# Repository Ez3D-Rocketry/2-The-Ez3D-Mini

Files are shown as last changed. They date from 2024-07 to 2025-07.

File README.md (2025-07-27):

# Ez3D-Mini

- Great park flyer that uses mini A motors
- Parts tape together
- No glue required

# Parts List:
1. Ez3D-1350-4 Fin Can
2. BT-50 Nose Cone
3. 13mm Retainer Cap
   - Print out the multiple sizes (No scaling, +3%, +5%), These account for different printing tolerances and post flight shrinking.
4. Six (6) inches of BT-50 type body tube
   - A standard 18 inch tube makes three kits
   - 3D printable tube cutting guide included in repository files
5. Three (3) feet of Kevlar string for Recovery Harness
   - Flight tested on 9KM DWLIFE Black Braided Kevlar Cord (1.3mm, 300 lb) but others may work
6. Twelve (12) inches of streamer (Optional)
7. Tape



# Assembly: 
     
1. Tie Recovery Harness to hole in Fin Can
2. Thread Recovery Harness thru Body Tube
3. Slide Body Tube onto top of Fin Can
4. Tape Body Tube to Fin Can - avoid blocking integrated launch lug
5. Tie loose end of Recovery Harness to Nose Cone
6. Tie streamer to Recovery Harness near top of Nose Cone

**NOTE: Individual printers and filament have different tolerances** <br />
**- Fit check items before assembly. Options to adjust if necessary:**
- Add tape to increase diameter
- Remove material by sanding
- If your printer has a scaling feature, use it to adjust the part size
- Change the dimensions in the FreeCAD file



# Launch Preparation:
1. Insert 1 or 2 squares of recovery wadding into Body Tube
2. Load Recovery Harness and Streamer into Body Tube
3. Place Nose Cone on top of Body Tube - ensure slightly snug fit
4. Load motor into Fin Can
5. Screw Motor Retention Cap onto base of Fin Can
   - Depending on your printer, the larger sizes may fit better
   - After a flight or two, the smaller size may fit better
6. Launch using standard model rocket procedures

# Recommended motors and expected performance: 

1/2A3-2T   = 93 ft  (Optimum delay = 2 s)

A10-3T      = 240 ft (Optimum delay = 2.95 s)

A3-4T       = 273 ft (Optimum delay = 3.3 s)

# IMPORTANT POST FLIGHT NOTES:
- 3D printed material shrinks after cooling down from heat of motor
- Removal of motor may be difficult or impossible after one or several flights
- The smaller motor retainer cap may fit better after the first flight
- If existing motor retainer caps no longer work, friction or tape may suffice for retention
- PLA filament most suspectable to shrinking. Others may last longer.

## Entire kit fits in a Ziplock sandwich bag!



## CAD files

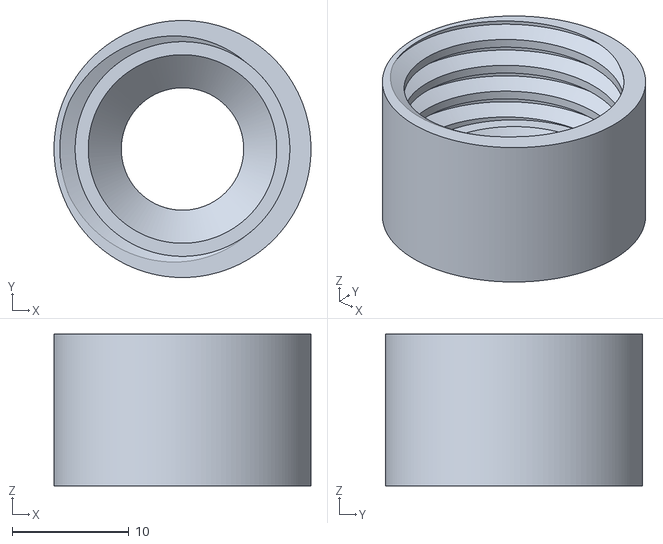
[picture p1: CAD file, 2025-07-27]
3D Printing Files/13mm Retainer Cap M20x2-13mmTall x1.05 in X and Y.stl
22.0 x 22.0 x 13.0

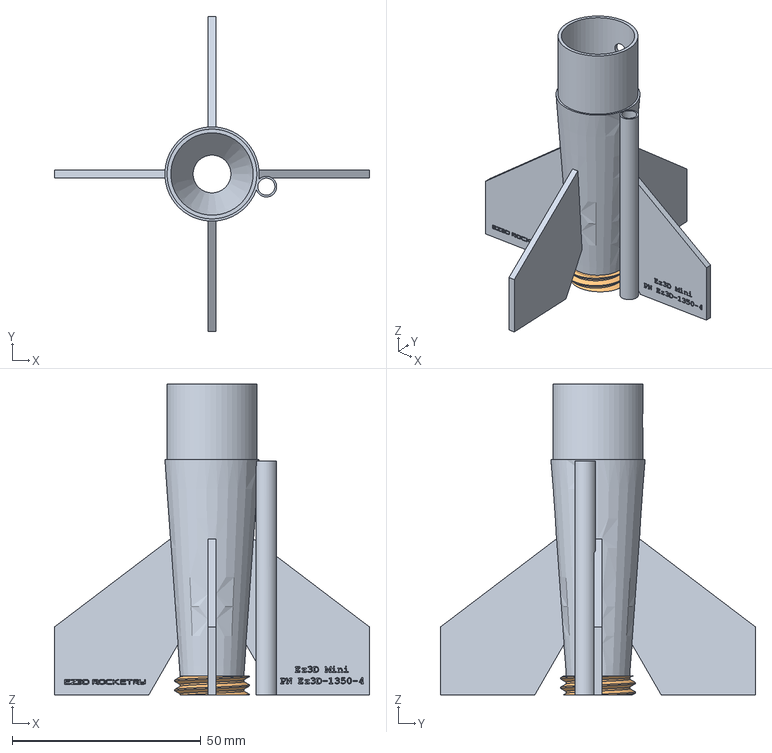
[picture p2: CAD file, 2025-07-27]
FreeCAD Files/Ez3D-1350-4 Fin Can.FCStd
83.5 x 83.5 x 82.3 mm
13mmThread20x2.5-5mmTall

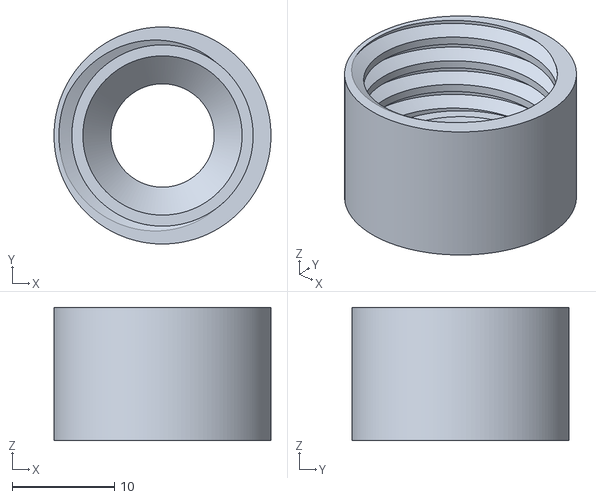
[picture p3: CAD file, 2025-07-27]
3D Printing Files/13mm Retainer Cap M20x2-13mmTall x1.01in X and Y.stl
21.2 x 21.2 x 13.0

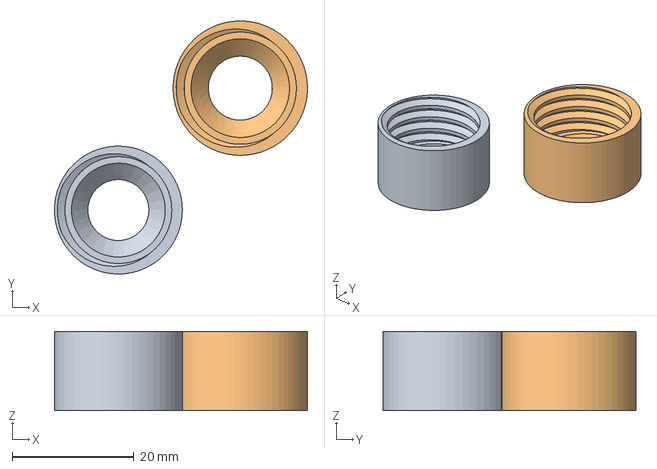
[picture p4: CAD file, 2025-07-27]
FreeCAD Files/13mm Retainer Cap M20x2-13mmTall.FCStd
41.5 x 41.5 x 13.0 mm
Use this Clone to make scaled up versions

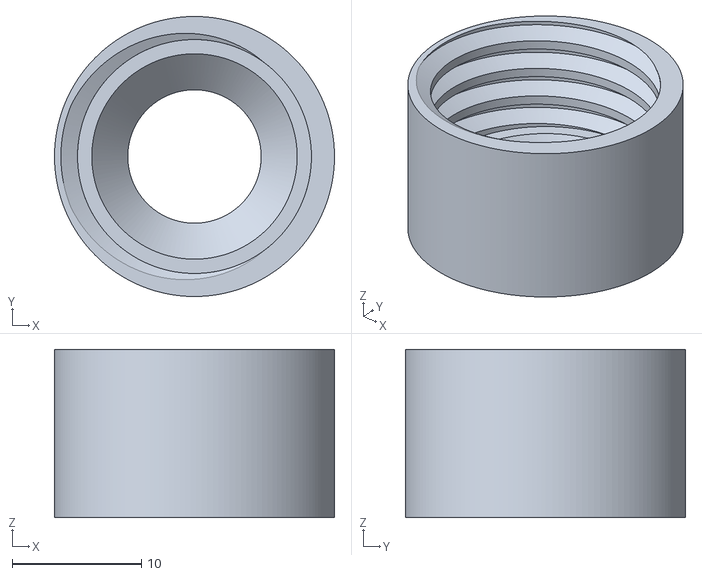
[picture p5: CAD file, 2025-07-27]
3D Printing Files/13mm Retainer Cap M20x2-13mmTall x1.03 in X and Y.stl
21.6 x 21.6 x 13.0

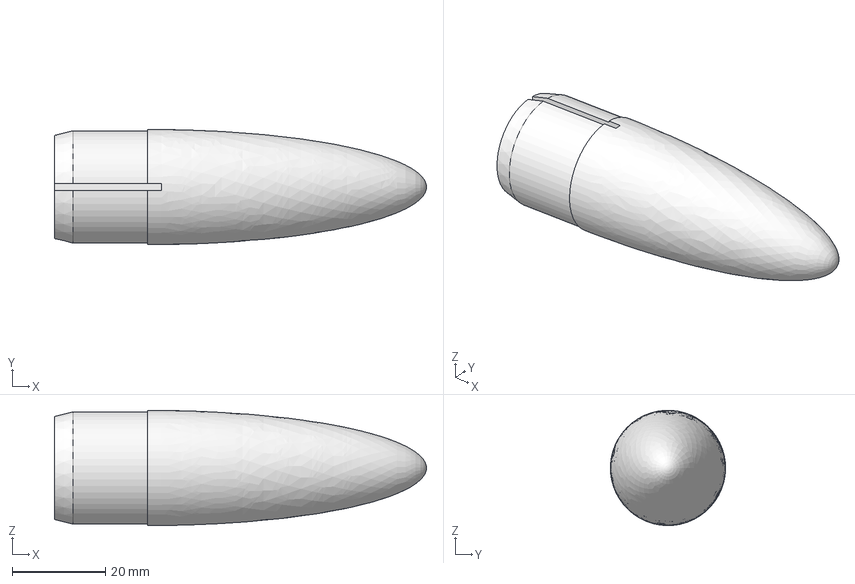
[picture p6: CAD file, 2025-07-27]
FreeCAD Files/BT50 Nose Cone - Elliptical, Hollow, with slot.FCStd
80.0 x 24.8 x 24.8 mm

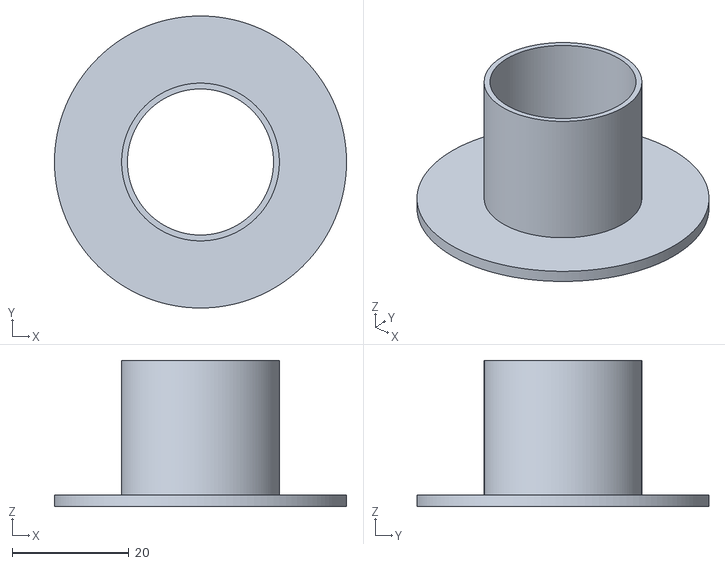
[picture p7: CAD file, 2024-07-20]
3D Printing Files/BT50 Tube Cutting Guide.stl
50.0 x 50.0 x 25.0

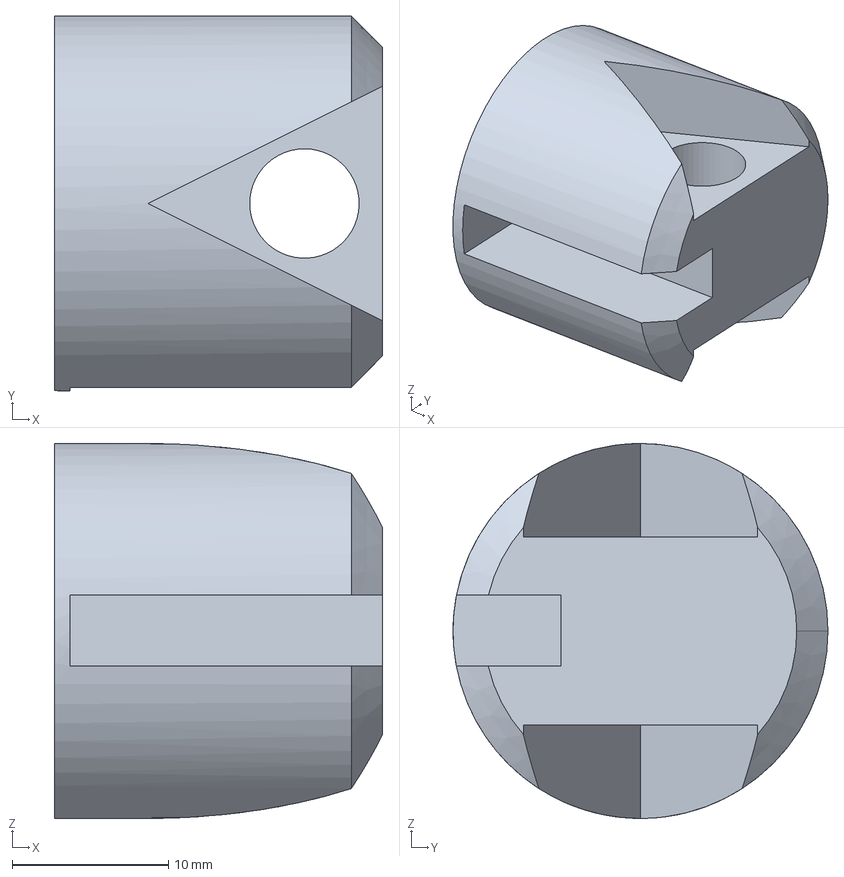
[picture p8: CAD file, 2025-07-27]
FreeCAD Files/BT50 Nose Cone - Elliptical, Solid, with slot.FCStd
21.0 x 24.0 x 24.0 mm

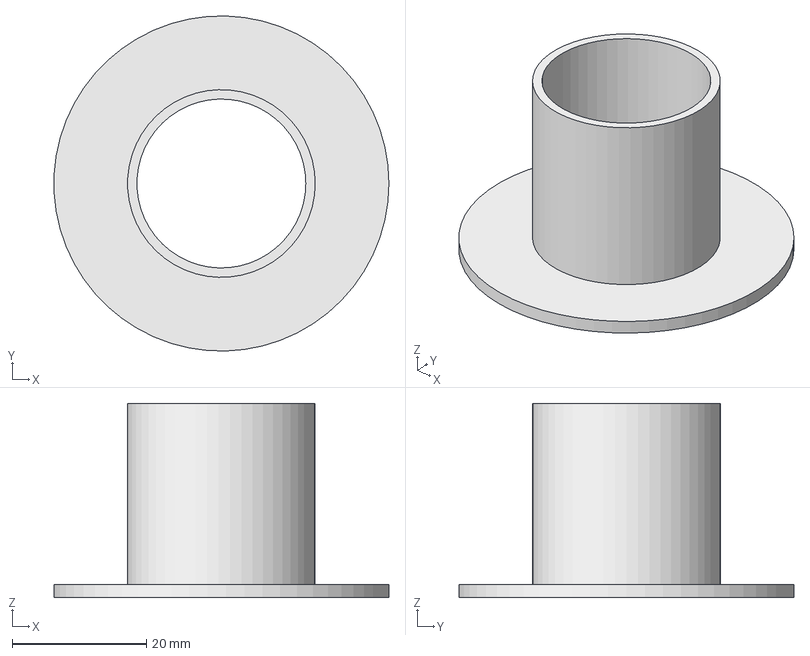
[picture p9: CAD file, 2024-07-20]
FreeCAD Files/BT50 Tube Cutter Guide.FCStd
50.0 x 50.0 x 29.0 mm

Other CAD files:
3D Printing Files/BT50 Nose Cone - Elliptical, Hollow, with slot.stl
3D Printing Files/BT50 Nose Cone - Elliptical, Solid, with slot.stl
3D Printing Files/Ez3D-1350-4 Fin Can.stl

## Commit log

2024-07-20 Rename BT50 Tube Cutter Guide.FCStd to _BT50 Tube Cutter Guide.FCStd
    [_BT50 Tube Cutter Guide.FCStd]
2024-07-20 BT-50 Cutting Guide FreeCAD file
    [BT50 Tube Cutter Guide.FCStd]
2024-07-20 BT-50 Cutting Guide STL file
    [BT50 Tube Cutting Guide.stl]
2024-08-03 BT50 Nose Cone - solid with threading hole STL file
    [BT50 Nose Cone - solid with threading hole in base.stl]
2024-08-03 BT50 Nose Cone - solid with threading hold - FreeCAD file
    [BT50 Nose Cone - solid with threading hole in base.FCStd]
2024-08-03 BT50 Nose Cone - simple threading hole STL file
    [BT50 Nose Cone - simple threading hole.stl]
2024-08-03 BT50 Nose Cone - simple threading hole FreeCAD file
    [BT50 Nose Cone - simple threading hole.FCStd]
2024-08-03 BT5 Tube Cutter Guide STL file
    [BT5 Tube Cutter Guide.stl]
2024-08-03 BT5 Tube Cutter Guide FreeCAD file
    [BT5 Tube Cutter Guide.FCStd]
2024-08-03 13mm motor retainer FreeCAD file
    [13mm Retainer Cap M20xReg-13mmTall label on side.FCStd]
2024-08-03 13mm motor retainer - orig size (smallest)
    [13mm Retainer Cap original size (smallest).stl]
2024-08-03 13mm motor retainer scaled up 3% in X and Y
    [13mm Retainer Cap scaled up 3 percent in X and Y.stl]
2024-08-03 13mm motor retainer scaled up 5% in X and Y
    [13mm Retainer Cap scaled up 5 percent in X and Y.stl]
2024-09-29 Update README.md
    Added comment about tapered motor mount tube after fight testing
2024-09-29 Delete Ez3D-Mini-FinCan.FCStd
    Replaced with tapered motor mount tube version
    [Ez3D-Mini-FinCan.FCStd]
2024-09-29 Delete Ez3D-Mini-FinCan.stl
    Replaced with tapered motor mount version
    [Ez3D-Mini-FinCan.stl]
2024-09-29 Ez3D Mini Fin Can files
    Added taper to motor mount tube to mitigate motors getting stuck due to material shrinking
    [Ez3D-Mini-FinCan.FCStd, Ez3D-Mini-FinCan.stl]
2024-10-13 3D printing files
2024-10-13 Rename BT50 Tube Cutting Guide.stl to 3d printing files/BT50 Tube Cutting Guide.stl
    [BT50 Tube Cutting Guide.stl]
2024-10-13 Rename BT50 Nose Cone - simple threading hole.stl to 3D printing Files/BT50 Nose Cone - simple threading hole.stl
    [BT50 Nose Cone - simple threading hole.stl]
